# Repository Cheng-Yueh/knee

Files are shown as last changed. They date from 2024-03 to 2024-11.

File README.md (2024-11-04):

# A Multi-Modal, Selectively Lockable, Compact, Affordable Knee Joint Assembly for Bipedal Robots

Welcome to the repository for making your own knee joint concept demonstrator designed specifically for bipedal robots! The files provided here permit reproducing the knee joint as presented in 2024 IEEE-RAS International Conference on Humanoid Robots conference. A video demonstrating the performance of this knee assembly is available at https://youtu.be/-a_vLSxSMBE.

### Key functionalities:
*	Actuated bidirectional joint rotation
*	Disengaged (neutral) or active transmission modes
*	Backdrivable
*	Joint lockable when fully extended, and can remain locked without consuming any energy

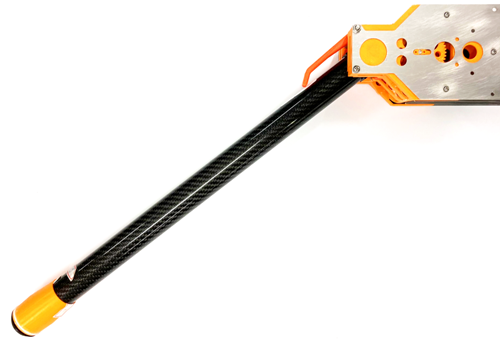
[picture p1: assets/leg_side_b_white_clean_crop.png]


## Mechanical hardware summary
To make things accessible for as many as possible, the design focuses heavily on field deposition modeling (FDM) 3D printable parts using a single extruder. Other items, like specialty parts, are described below. Fasteners are depicted in the CAD model. Mechanical and electronics assembly guidelines are provided separately. Refer [/CAD](CAD/).

### Manufactured parts
These mechanical parts do require workshop fabrication:
| Name (in CAD) | Description | Quantity | Details |
| --- | --- | --- | --- |
| KNEE_BRACE_3 | Chassis plate A | 2 | 1 mm SS304, laser cut |
| KNEE_BRACE_OUTER_V3 | Chassis plate B | 2 | 1 mm SS304, laser cut |
| KNEE_PIN_V3 | Knee lock pin bolt | 1 | SS304, CNC milled |
| KNEE_INNER_2B_V5 | Knee pivot | 1 | AL7050/7075, anodized, CNC milled |

### Bearings and bushings
| Name (in CAD) | Description | Quantity | Details |
| --- | --- | --- | --- |
| SKF - 61803 | Joint ball bearing | 2 | Can use 6803ZZ or alternatives |
| H370FI-0405-06 | Pin bolt sleeve | 1 | IGUS® bushing |
| H370SI-0405-06 | Pin bolt receptacle | 1 | IGUS® bushing installed in knee pivot |

### Actuators
| Name (in CAD) | Description | Quantity | Details |
| --- | --- | --- | --- |
| MOTOR_140 | Type 140 motor | 4 | Mabuchi RE-140RA-12240 or equivalent |
| SOLENOID_SH_K0730 | Latching solenoid | 1 | Shih Shin SH-K0730S-06V |

You will need to source a suitable spring (or two) for the latching solenoid. An example design is provided [here](CAD/SPRING.PDF).

## Electronics summary
Schematics and Gerber files to let you DIY electronics presented in the conference paper are provided in [/electronics](electronics/). The associated Python code (executable on a Raspberry Pi) are available in [/code](code/). Prescribed methods piggyback on 5V I2C communication protocol; remember to include a level shifter if using a Raspberry Pi. Shielded cabling mitigates EMI. However, you can use any method to operate the knee joint. Feel free to adapt and use your own devices if desired.

### Motor and solenoid driver (DRIVER_KNEE_V5)
Select your own feedback current resistor values (R<sub>FB</sub>) corresponding to R_M1 to R_M4 on the schematic. These should be populated – even if you do not intend to measure current. Nominal values provided are for reference only.

### Knee joint angle sensing (ENCODER)
A small radial magnet is necessary to complement this Hall-effect sensor. Adapt the CAD files as necessary for the magnet you acquire.

## Comments or suggestions
[Submit a ticket](https://github.com/Cheng-Yueh/knee/issues)

IMAGE ALT TEXT HERE (https://www.youtube.com/watch?v=-a_vLSxSMBE)

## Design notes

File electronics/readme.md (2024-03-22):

# Electronics
Custom electronics were devised for driving this open source product. Two relevant PCBs are:
*	Joint angle sensor (ENCODER): acquires the absolute angular position of the knee using a Hall-effect IC.
*	Motors and solenoid driver (DRIVER_KNEE_V5): independently maintains constant actuation using built-in PWM functionality. Output current could be estimated on each of the four motor H-bridge channels.

Both devices are managed using I2C (SMBus) protocol. Get your PCB and solder mask made with files in [/GERBER](GERBER/). Reflow soldering is recommended for the surface mount devices. Advise processing bottom layer before top layer. Refer [soldering schematic PDF](Soldering%20Schematics.pdf).

Alternatively, modify and adapt the mechanical CAD model to suit your own electronics as you wish.

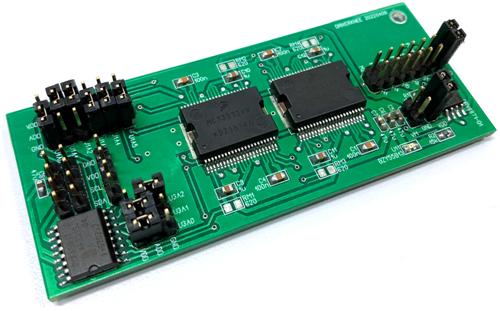
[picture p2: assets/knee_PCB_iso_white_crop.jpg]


## ICs used
The tables exclude passive or connector components.

### DRIVER_KNEE_V5
| IC name  | Description | Footprint | Quantity |
| --- | --- | - | - |
| PCA9685PW  | 16-channel, 12-bit PWM Fm+ I2C-bus LED controller  | TSSOP28 | 1 |
| PCF8591T  | 8-bit A/D and D/A converter  | SO16W | 1 |
| MC33932VW | 5.0 A throttle control H-bridge | HSOP44 | 2 |
| DRV8871-Q1 | 3.6-A Brushed DC Motor Driver With Internal Current Sense (PWM Control) | HSOP8 | 1 |
### ENCODER
| IC name  | Description | Footprint | Quantity |
| --- | --- | - | - |
| AS5048B  | Magnetic Rotary Encoder (14-Bit Angular Position Sensor) | TSSOP14 | 1 |

## DRIVER_KNEE_V5 wiring
Motor [wiring configuration](Wiring%20Configuration.pdf) is separately outlined, which is compatible with the Python code provided. Other connections are tabulated below.

| PCB label | Connect to | Component | Remarks |
| --- | --- | --- | --- |
| M1 to M8 | Motor pins | DC motors | Refer Wiring Configuration.pdf |
| S1 | Red (+) wire | Latching solenoid | Refer manufacturer datasheet |
| S2 | Black (-) wire | Latching solenoid | |
| VM | 12: 24V<br>GND: ground | Power supply | Intended for 12V but 24V compatible |
| VDD | 5: 5V<br>GND: ground | | |
| U1A0 to U1A5 | | Jumpers | Programmable I2C slave address for PCA9685PW |
| U3A0 to U3A3 | | Jumpers | Programmable I2C slave address for PCF8591T  |
| SDA | I2C data line | Computer/ microcontroller | |
| SCL | I2C clock line | Computer/ microcontroller | |
| GND | Ground | | Common I2C and VM ground |

## Caveats
* All electronics could be manually soldered by hand. Any thermal pads underneath ICs must be connected!
* Prepare suitably long cables. Excessive lengths may require I2C capacitance buffers / accelerators. Too short and you will experience poor cable management.
* Plan cable connection points to facilitate modular (dis)assembly.

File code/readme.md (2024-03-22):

# Code overview
The default electronics provided can be operated using a Raspberry Pi using these Python files:
* driver_public.py: drives the actuators (motors and latching solenoid).
* encoder.py: retrieves joint angle readings from AS5048B.
* pcf8591_public.py: retrieves raw ADC values for motor current estimation.

## Usage
Recommended function APIs are documented below; helper functions are not included.

### driver_public.py
#### `initialize(PCA9685_add)`
Initializes the PCA9685PW PWM IC with default settings.

Parameters
*	PCA9685_add(int): I2C address.

Returns None

#### `set_PWM_freq(PCA9685_add, freq)`
Sets the desired PWM frequency of PCA9685PW to drive H-bridges.

Parameters
*	PCA9685_add(int): I2C address.
*	freq(int): PWM frequency in Hz.

Returns None

#### `set_knee(PCA9685_add, func, duty, duty_max = 0.25, duty_lambda = 1, duration = None)`
Actuates the knee motors with specified mode of operation.

Parameters
*	PCA9685_add(int): I2C address.
*	func(int): knee joint operation mode. 0: flexion (bend knee); 1: extension; 2: disengage transmission; 3: engage transmission.
*	duty(float): PWM motor duty (0 to 1).
*	duty_max(float): maximum permissible PWM motor duty (0 to 1) regardless of duty(float).
*	duty_lambda(float): duty prescaler (0 to 1) to impart a net downward compound transmission gear force using differential PWM motor duties.
*	duration(float): operation time in seconds; motors will turn off after duration.

Returns None

#### `set_solenoid(PCA9685_add, mode, duration=0.1, lock_duty = 1.0, unlock_duty = 0.5)`
Actuates the latching solenoid knee lock.

Parameters
*	PCA9685_add(int): I2C address.
*	mode(int): 0: lock; 1: unlock.
*	duration(float): operation time in seconds; solenoid will turn off after duration.
*	lock_duty(float): lock mode PWM duty (0 to 1).
*	unlock_duty(float): unlock mode PWM duty (0 to 1).

Returns None

### encoder.py
#### `read_angle(output = 'bit', offset = 0, remap = True, enc_add = ENC_ADD)`
Returns the absolute knee joint angle.

Parameters
*	output(str): 'bit': returns angle in raw bit value; ‘deg’: returns angle in degrees; ‘rad’: returns angle in radians.
*	offset(float): returns the angle relative to a prescribed offset value.
*	remap(bool): True: remaps angle equivalent to -180° < value ≤ 180°.
*	enc_add(int): I2C address.

Returns int if output == ‘bit’, else float

### pcf8591_public.py
#### `set_mode(auto_inc = None, channel = None, PCF8591_add = PCF8591_ADD)`
Initializes the ADC scanning mode, and returns the associated configuration mode value.

Parameters
*	auto_inc(bool): True: sets ADC to automatically increment return values over each channel as defined in IC datasheet; False or None: disables ADC auto increment.
*	channel(int): sets a single ADC channel (0 to 3) for returning values. Refer to IC datasheet.
*	PCF8591_add(int): I2C address.

Returns int

#### `get_adc_values(mode = MODE, n = 1, PCF8591_add = PCF8591_ADD)`
Reads and returns ADC values.

Parameters
*	mode(int): ADC scanning mode configuration value.
*	n(int): number of times to read the ADC with defined mode.
*	PCF8591_add(int): I2C address.

Returns list

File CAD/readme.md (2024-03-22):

# Mechanical assembly
The prescribed assembly is available as Parasolid format (LEG_ASSY_2_PUBLIC.x_t). Construction order should be quite self-explanatory; there is no single best method, which lends to modular flexibility. In general:
*	Prepare ALL electronics and wiring in advance.
*	Build the knee joint from inside core to the outside.
*	Use various strength threadlocker (or none at all) in lieu of nyloc nuts.
*	Cable conduits and holes throughout the CAD model facilitate different wiring combinations depending on application. Use them wisely.

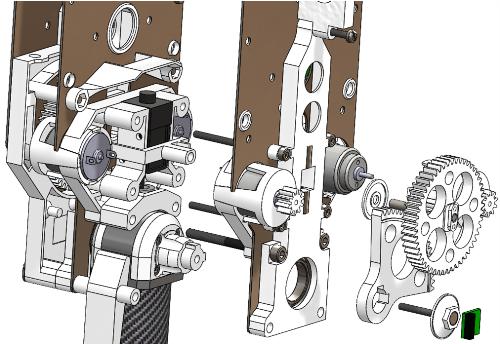
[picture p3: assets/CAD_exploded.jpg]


## FDM suggestions
Field deposition modeling (FDM) for 3D printing plastic parts presented in this product is preferred. Ultraviolet stereolithography (SLA) methods are not advised due to poor structural strength. 30% infill using polylactic acid (PLA) should be more than adequate for most parts. Consider up to 60% infill for knee pivot components experiencing concentrated stresses.

## Lubrication
All transmission components should be lubricated with elastomer-polytetrafluoroethylene gelling agent and parafiinic mineral base oils. These grease compounds do not react with FDM plastics such as PLA, facilitating stable and low maintenance operation.

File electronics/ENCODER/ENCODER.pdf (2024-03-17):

VDD5V

1
2

1

### 2 U2 HEADER2

C1 47u

## Cheng-Yueh Liu ENCODER rev: 15 March 2024

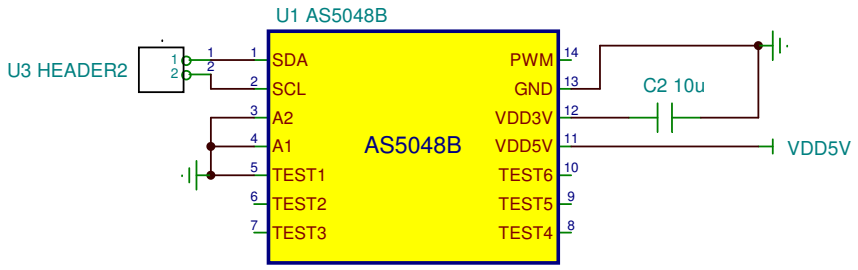
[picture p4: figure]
VDD5V; U3 HEADER2; PWM; GND; VDD3V; TEST6; TEST5; TEST4; SDA; SCL; TEST1; TEST2; TEST3

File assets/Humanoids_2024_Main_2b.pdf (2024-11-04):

On the Development of a Multi-Modal, Selectively Lockable, Compact,

## Affordable Knee Joint Assembly for Bipedal Robots

Cheng-Yueh Liu¹

, Jaspreet S. Dhupia¹

, Minas Liarokapis¹

, and Pei-Chun Lin²

Abstract— Contemporary advances in humanoid bipeds include complicated mechanisms supporting fully actuated robotics. While these solutions offer unprecedented versatility that relies on sophisticated locomotion systems, the efficient traversing capabilities of natural, passive-inspired gait may be overlooked. In this paper, we focus on the development of a disengage-able, selectively lockable, affordable knee joint assembly suitable for either active or underactuated biped operation. The multi-modal nature of the design facilitates actuated bidirectional rotation as well as disengaged operation, while the knee lock ensures legs remain rigid during stance phase. Experimental validation of the performance of the knee assembly demonstrated both controllable knee joint actuation and fully passive rotation, various modes of operation, and torque evaluations. Further investigations include validation testing of operational and locking performance on a physical bipedal robot. System parameter optimizations can reduce energy consumption. The design proved feasible and is opensourced to facilitate replication and co-development with others.

I. INTRODUCTION

Bipedal robots are characterized by an unparalleled versatility, leveraging their advanced human-like locomotion capabilities that allow them to traverse dynamic and unstructured human-oriented environments. These systems must include a mechanism that reduces effective hip-foot length. A knee joint mechanism provides such capability in humanoids, which is essential to prevent foot scuffing during leg swing phase. The rear leg can rotate forward without the feet hitting the ground. However, many implementations try to achieve the most overpowered solution for utmost capability, which obfuscates elegance and basic requirements in simple bipedal gait. Through appreciating fundamental paradigms, the proposed knee supports first principles evaluation and potential transfer of natural human gait for efficient robot walking. A simple and low cost design promotes mass replication and widespread adoption within the robotics community.
A basic kneed walker could be modelled as a planar biped depicted in Figure 3. An upper body linkage manipulates robot center of mass (CoM) in the sagittal plane to initiate gait. Such configuration biomimics human physiology and can be considered as a template in biped robotics development. Although different postures during walking are possible, the most fundamental gait in Figure 2 provides a basis for which variations could be built upon. Under these

1Cheng-Yueh Liu, Jaspreet S. Dhupia, and Minas Liarokapis are with the Department of Mechanical and Mechatronics Engineering, The University of Auckland. Emails: cliu695@aucklanduni.ac.nz, j.dhupia@auckland.ac.nz, minas.liarokapis@auckland.ac.nz
2Pei-Chun Lin is with the Department of Mechanical Engineering, National Taiwan University, Taiwan, ROC. Email: peichunlin@ntu.edu.tw

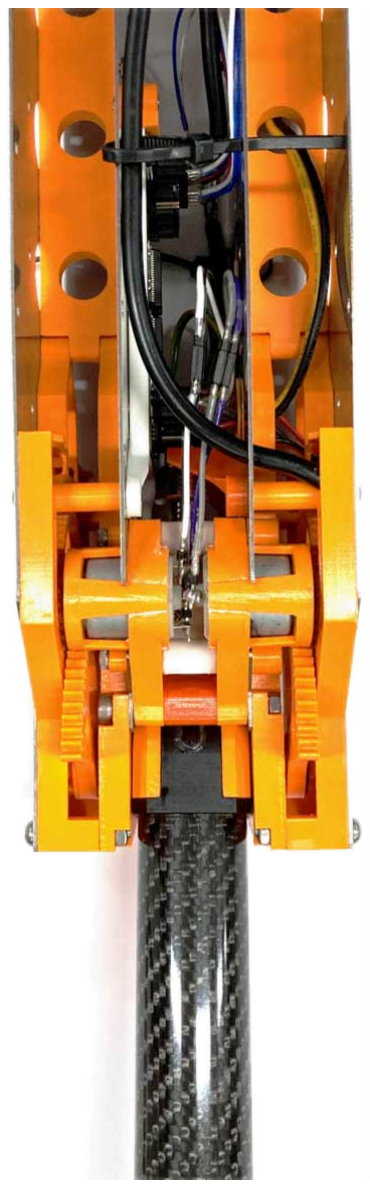
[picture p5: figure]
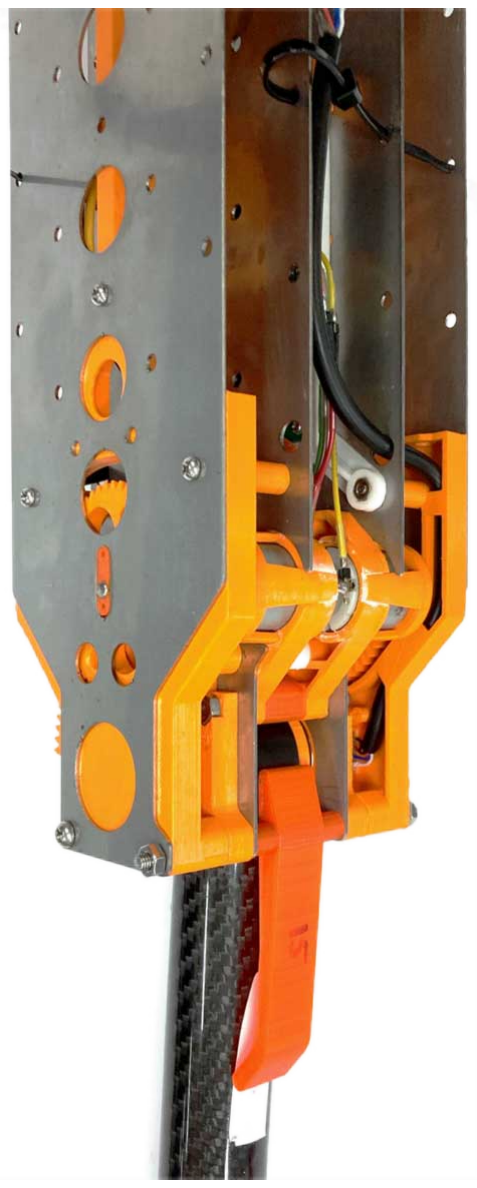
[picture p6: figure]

Fig. 1. The proposed knee joint assembly. Subfigure a) presents the rear view and subfigure d) presents the isometric view. All associated mechanisms, actuators, and electronics presented throughout the paper are integrated within the depicted assembly. The near symmetrical layout across both sagittal and coronal planes, facilitates an even distribution of inertia and mass.

circumstances, the knee of stance (dotted) leg remains locked and rigid.
Therefore, the sole purpose for knee bends of the rear swing leg is preventing foot scuffing. Such gaits do not require knees to exert much torque (if any) requiring little actuation. This effect is further accentuated should lower limb extremities, consisting of shank and foot, possess minimal mass and rotational inertia about the knee.
The Lagrange dynamic model describing biped motion of the configuration in Figure 3 is found to be
D(θ)θ¨ + h(θ, θ˙) + G(θ) = τ | (1)

where
θ | = [θ1, θ2, ..., θ5]

T
,
τ | = [τθ1, τθ2, ..., τθ5] | T ,

h(θ, θ˙) = col[
P
| 5
| j=1(j̸=i)

(hijj (

| | ˙θj )
| | 2
],
G(θ) | = col[Gi(θ)],
D(θ) | = [Dij (θ)], | i, j = 1, 2, ..., 5.

(2)

Here D(θ) is the 5 × 5 symmetric, positive definite

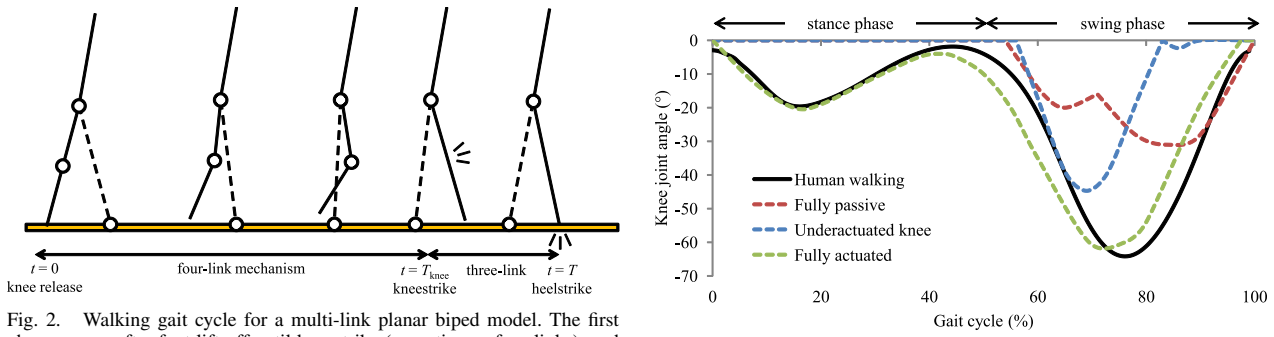
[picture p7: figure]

Fig. 2. Walking gait cycle for a multi-link planar biped model. The first phase occurs after foot lift-off until kneestrike (operating as four links), and the second phase continues until heelstrike as a two-link mechanism.

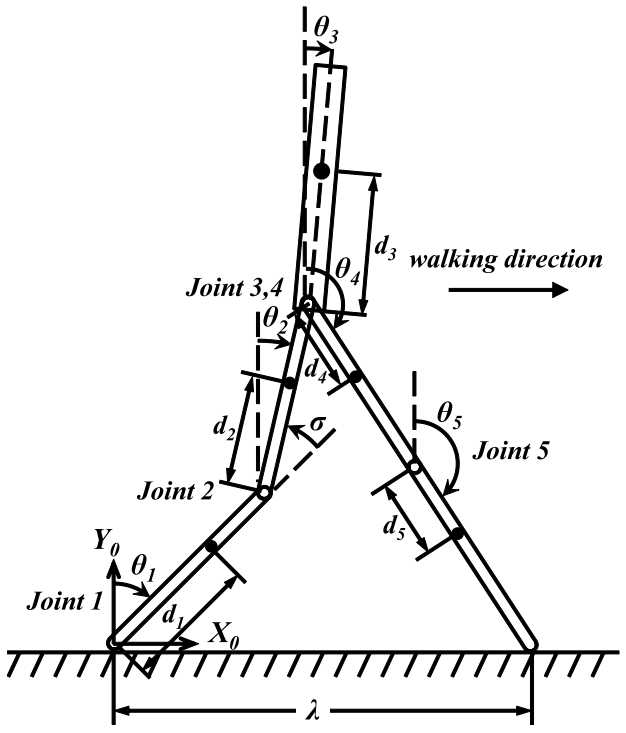
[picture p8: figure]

Fig. 3. Nomenclature of a 5-link planar biped robot suitable for the proposed knee joint. By manipulating upper body angle θ3, the robot can commence walking when center of mass is ahead of stance (front) foot.

inertia matrix, h(θ, θ˙) is the 5 × 1 vector of centripetal and Coriolis forces, G(θ) is the 5 × 1 vector representing gravitational forces, and τ is the 5 × 1 generalized torque vector corresponding to θi
. A full derivation [1] and equations during heel and knee strike switching events [2] are well documented.
Figure 4 portrays generalised knee angles, which never exceed -70°, during comfortable human walking and compares that with various biped setups. Physiologically, the human knee does undergo slight flexion during stance. Passive dynamic walkers can be classed as legged machines for which dynamic walking occurs naturally. By offering a clutch for transmission engagement and disengagement, natural bipedal dynamics can be combined easily with active energy input so as to produce efficient and versatile walking over

Fig. 4. Representative knee angles of human vs select biped robot topologies during walking. Flexion angles are negative. Comfortable human walking speed = 1.24 m/s, stride length (2λ) = 1.32 m. Graph constructed as a composition from existing graphs in [3]–[5]; human knee flexion angles collated using averages of comfortable gait data in [6].

a broad range of unstructured terrains [7]. Another category of simple walking machines, underactuated bipeds, can take advantage of upper-body control, resulting in efficient limitcycle gaits by avoiding generation of negative input power [8]. Moreover, robots that harness passive dynamics use less control and energy than other powered robots, yet walk more naturally [9]. Through actively controlling the hip, knee joints can be underactuated during the locomotive gait. Previous underactuated or passive dynamic walkers lock their knees straight throughout stance phase. Table I provides an overview of knee functionalities in fully passive, underactuated and fully actuated biped setups. In [10] Etoundi, et al. reviewed various biomimicking knee joints and identified general trends. For example, a bio-inspired knee joint incorporated planetary gearing with pneumatic artificial muscles actuating a compound sun gear pulley [11]. Another design consists of a crossed four-bar linkage with variable transmission and a joint stop proposed in [12]. The remainder of this paper is organized as follows: Section II divulges on the inspiration behind the mechanical design, Section III discusses in detail how the proposed transmission mechanism works and custom electronics, Section IV presents the experimental validation of the efficiency of the proposed knee assembly, while Section V concludes the paper and discusses future directions.

II. DESIGN INTENT

A disengageable transmission facilitates controlled passive walking. For the most elementary geared knee clutch, the decoupling of joints to any actuation transmission enables underactuation and exhibit passive dynamics [19]. Such natural movements form an ideal scenario whereby a robot could harness the ultimate manifestation of energy efficiency, coupled with a fully actuated or backdrivable joint when necessary.
Hip joint actuation is by far the main power contributor for sustaining forward gait locomotion [8], [9]. In this context, it is feasible to derate (or underpower) the knee joint as much as possible. The knee need not contribute torque for forward motion and can be locked during stance. Positioning the knee

TABLE I

VARIOUS KNEE ACTUATION TOPOLOGIES FOR A HUMAN-INSPIRED WALKER.

Type | Fully passive | Underactuated knee | Fully actuated

Example image

Description | Passive dynamic walkers walks down slope without any actuation. Powered by gravity. | Robot with passive-inspired elements and actuated hip. Walks on flat sur-face. | All relevant degrees of freedom are actively controlled with actuators, in-cluding knees and hip joints.
Select examples | Dexter, robots by Garcia/McGeer, Ru-ina/Collins [3], [7], [9] | Dribbel, Denise [13], [14] | ASIMO, Atlas, NAO, Veronica, RoK-4 etc. [15]–[17]
Knee design | No active actuation. Knee flex-ion/extension occurs naturally during gait. | Active knee locking mechanism. Knee rotation not actuated. | Knee joint directly actuated via per-manent transmission. May use adapt-able or compliant joints. [18]
Angle range | 0° to -35° typ | 0° to -50° typ | 0° to -65° typ
Knee torque performance | 0 Nm | 0 Nm | Varies greatly depending on robot.
Knee lock | May incorporate passive knee locking mechanism for stance phase. | Electromagnetic, voice-coil, motor or solenoid driven etc. | Under-actuated examples plus clutch variations coupled to active transmis-sion.
Passive mode | Yes | Yes | No
Controllable flexion | No | No | Yes

TABLE II

KNEE DESIGN SUMMARY AND PHYSICAL PARAMETERS OF TEST SHANK.

| Variable | Value
Angle range | -σ | 0° to -70°
Knee lock | | Latching solenoid
Mechanism mass | | 470 g
Passive mode | | Yes
Controllable flexion | | Yes
Shank length | d1 + d5 | 0.45 m
Shank mass | (Link 1) | 0.09 kg
Foot mass | Joint 1 | 0.04 kg
Moment of inertia about knee | | 0.0142 kg m²
Shank CoM | d1 | 0.1558 m

actuators nearer the hip with mechanisms, such as linkages or cables, for transmission [20] add complexity and mass. A lightweight knee joint reduces overall leg mass and inertia, which facilitates smaller hip joint torque requirements. During the stance phase, each knee must able to support its corresponding thigh, hip, and swing leg without bending. Such substantial loading would require knee exertion of significant torques during what should be a passive gait phase.

One straightforward actuation methodology is to mount a geared, inline motor directly at the knee joint with supporting elastic and damping elements [21]. However, with no locking mechanisms, energy is consumed to oppose bending torques using the employed actuator. Instead of relying on actuators, a separate knee locking mechanism, which does not consume energy to maintain state, is desirable. Plooij, et al. [18] identified properties an ideal robot joint locking device shall possess: i) adjustable locking directions, ii) ability to unlock while under load, iii) low energy consumption, iv) ability to lock in any position, v) short switching time, vi) high locking force and vii) be compact, lightweight, and inexpensive. Locks could be categorized by active or passive modes of operation, which include electromagnetic [22], permanent magnet [23] or the use of suction cups for lock activation. Reynolds [24] developed a differential-brake style clutch. However, passive knee locking mechanisms could lose synchronization with the gait cycle that can affect overall reliability.

III. MECHANISM DESIGN

A large speed reduction ratio is necessary to provide sufficient torque for actuating robot shanks [25]. The solution presented here uses a multistage gear reduction system incorporating a compound gear for an overall 40:1 gear reduction. The hardware is composed of subsystems incorporating a gearbox, lock, associated electronic drivers, and a rotary encoder (see Figure 5). The knee joint is actuated using

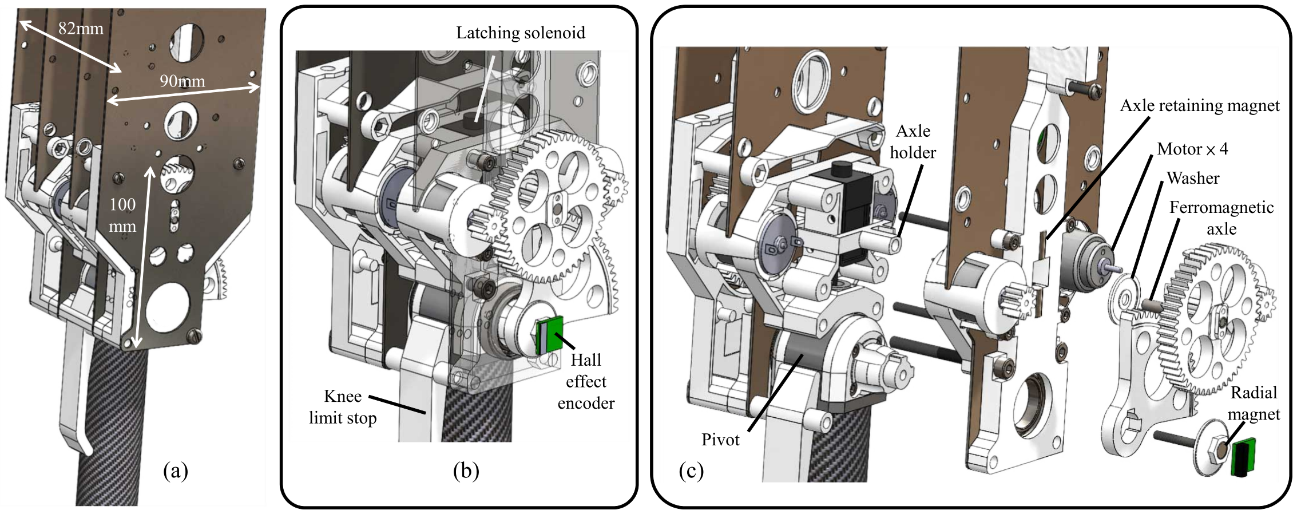
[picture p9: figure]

Fig. 5. Knee joint mechanism. Mass is 470g excluding chassis components. a) Overview. b) Cutaway view without side sheetmetal. c) Exploded view of left half, revealing axle holder, which can translate vertically about the latching solenoid in the inner core. Mechanism is symmetrical about sagittal plane.

a modified planetary gearbox transmission system that can
be disengaged for passive dynamics. An embedded bolt,
powered by a bistable or latching solenoid, keeps the shank either locked at a fixed angle (during stance phase) or unlocked without consuming any energy to maintain state (see Figure 6).
Serial elastic actuation elements were considered but omitted. Low transmission torque outputs mean elastic components must be soft, implying minuscule energy storage is obtainable. However, damping elements could be retrofitted to smooth stroke transitions at end limits.
A. Gearbox
In the proposed design, Type 140 brushed direct current (DC) motors, rated at 6V (Mabuchi RE140RA-12240 or equivalents), provide knee joint power at 80 g each. Four motors are arranged in a planetary fashion as depicted in Figure 6, without ring gear. Coupled to a compound sun gear, the two-stage transmission imparts a gear reduction of 50:10 and 80:10 respectively. Furthermore, each pair of motors is symmetrically positioned in both the sagittal and transverse planes. This deliberate organization ensures the mechanism imparts identical inertial distribution across both planes while promoting equal torque contribution from each motor.
B. Gearbox Doubles as Clutch
Each compound (sun) gear revolves between two, significantly smaller, planet gears placed diametrically opposite and horizontally 180° apart. Rotating the compound gear about a fixed axle transmits torque to bend the knee in either direction, which is achieved by synchronous operation of all four DC motors in tandem and rotating the joint. However, the transmission is deliberately designed so other modes of operation are possible if minor constraints are removed. When the sun gear axle is permitted to translate vertically upwards, by a lateral displacement marginally greater than the gear tooth depth, the compound gear is decoupled from the output (second gear set). This additional degree of freedom can be employed by contra-rotating the two planets in opposite directions. It is important to ensure the sun gear movement is restrained such that the teeth always mesh with planet gears. Therefore, four modes of operation become possible: i) transmission disengagement, ii) transmission engagement, iii) clockwise join actuation, and iv) counterclockwise joint actuation. Retaining the sun gear axle in the up or down position, for transmission disengagement or engagement respectively, can be achieved by any methodology deemed suitable in the actual application. For the purposes of this paper, permanent magnets are used in conjunction with a ferromagnetic axle. The two motors could also impart net up or down translational forces so as to assist in retaining the sun gear position. For example, when the axle is in down (engaged) position for knee rotation, both planet gears (and motors) are actuating in the same direction. Due to being positioned opposite each other, one of the planets will be invoking an upwards force when driving the sun gear teeth, but neutralized by the other planet exerting force downwards. By applying not only various voltages or duties, but also a differential, to the two motors while actuating the joint, both the net output torque and sun gear retaining force can be adjusted. By repurposing the very motors and gears used for joint actuation, the gearbox effectively doubles as a clutch. Simple yet innovative supplementary mechanics are important when pursuing elegant outcomes.
C. Joint Lock
Electromagnets or voice-coil actuated locks [13] consume substantial current (up to a few amperes) just to maintain state. A miniature latching solenoid (Shih Shin SH-K0730S-06V) [26] was identified so as to implement a linear boltlock configuration. These devices passively maintain a set position without constant application of electrical current. The latching solenoid linearly actuates a 6.3 mm bolt into the joint pivot, with 9 mm stroke for locking (Figure 6c).

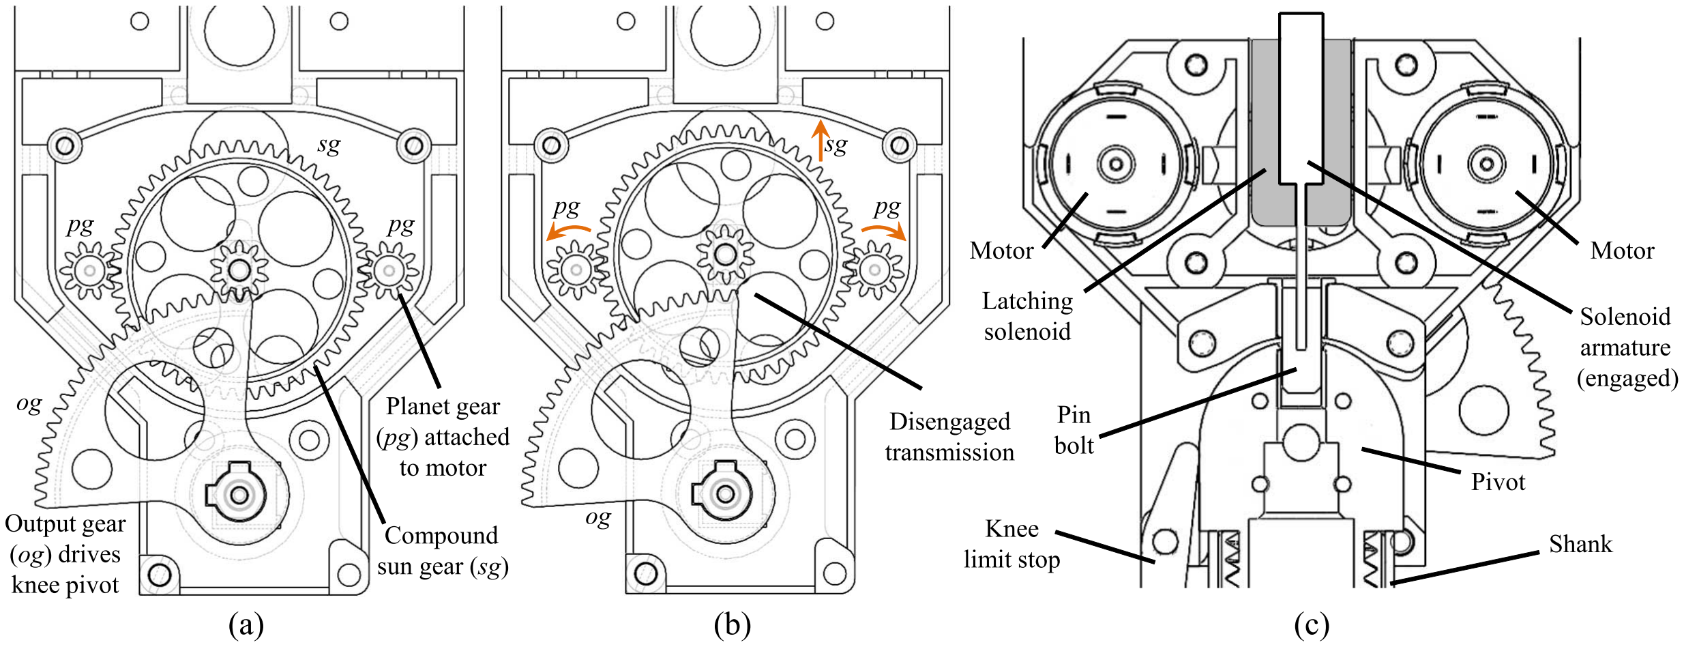
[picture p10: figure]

Fig. 6. Gearbox and knee lock. a) Engaged transmission; compound sun gear (sg) is down and mating with output gear (og) of knee pivot. b) Disengaged transmission; sg is up and floats above og. c) Knee lock mechanism with pin bolt engaged, preventing the pivot from rotating. The cross section is across lower limb sagittal plane.

TABLE III

KNEE DRIVER LOAD CURRENT ESTIMATION FOR SELECTED RF B .

RF B

aADC
(10⁻³)

bPWM

cconst
(10⁻³)

R

| | | | 2 | RMSE (10⁻³) | RSE (10⁻³)
4k7 | 1.09244 | 0.23724 | -10.9677 | 0.9972 | 4.6597 | 4.8732
10k | 0.52400 | 0.17088 | -7.80886 | 0.9997 | 0.9922 | 1.0501
22k | 0.24959 | 0.24924 | 2.80037 | 0.9997 | 1.1807 | 1.2623

To minimize friction and assist engagement, the pivot is press-fitted with an IGUS® H370SI-0405-06 self lubricated bushing which acts as the receptacle. A secondary IGUS® H370FI-0405-06 bushing supports the bolt on the fixed side. In practice, the fully assembled joint exhibits a maximum backlash of approximately 5° when locked. Liu, et al. [27] devised a tapered pin lock configuration, the shape of which removes fit clearance to prevent knee bending when engaged. Such provision for compliance is a reference for further mechanical refinements.

In order to actuate the aforementioned electromechanical DC motors and solenoids, custom made knee driver electronics have been developed. Programmable resistor/capacitor combinations, as described in the evaluation section below, generate voltages that estimate feedback current sensing characteristics of the four DC motors. An 8-bit analogue to digital converter (ADC) reads the associated voltage. Both the PWM generator IC and ADC employ I2C for data communications with the microcontroller unit. Finally, a 14 bit Hall-effect rotary encoder (AS5048) about the knee joint axis of rotation measures knee stance angle. A radial magnet is placed on one end a rotating axle (hidden), adjacent to the encoder. I2C interface is used throughout for bus commonality.

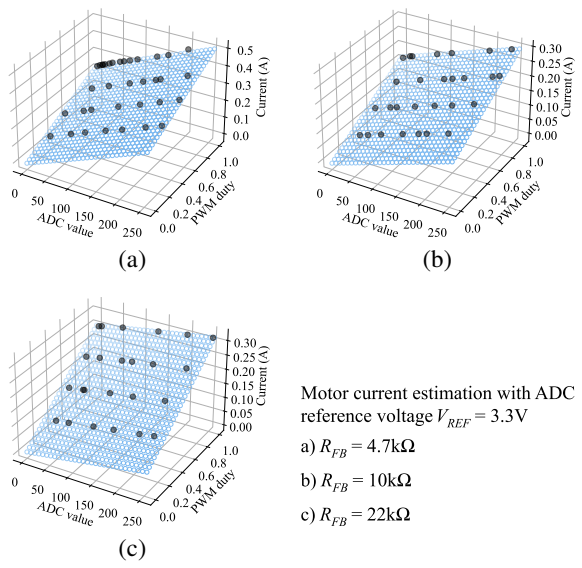
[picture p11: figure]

Fig. 7. Knee driver current sensing calibration with various feedback resistors (RF B). By choosing an appropriate value, full scale detection of motor current can be realized.

IV. EVALUATION

The proposed knee joint assembly is depicted in Figure 1. The shank (attached to the joint) is a carbon-fiber tube with a plastic “shoe” (see Figure 10). Apart from electromechanical actuators, knee pivot and bolt lock, all other mechanical parts are printed with fused deposition modeling using polylactic acid (PLA). Shank parameters and knee joint costings are listed in Tables II and IV respectively.

A. Motor Driver and Current Sensing

The knee motor driver PCB incorporates 8-bit current sensing capabilities. Current sensing calibration is required

TABLE IV

LISTED COST BREAKDOWN FOR ONE KNEE MECHANISM.

Item | USD
PLA material | 2
DC motors (four) | 8
Latching solenoid | 12
SS304 lock pin bolt (CNC) | 30
AL7075 knee pivot (CNC) | 180
Bearings | 15
Electronics | 60
Miscellaneous | 5
Total | 312

to understand the relationship between ADC readings, H-bridge PWM duty cycles, and actual (motor) load current for programmable current sensing resistor values (RF B). In this paper, tests were conducted with 1526Hz PWM frequency and slow decay (low side active freewheeling). Variable loads are connected directly to one knee driver H-bridge output with a multimeter in series. Results for RF B = 4.7k, 10k and 22k Ω are depicted in Figure 7.
Optimal RF B selection should produce full-scale ADC readings (0 to 255) across a range of expected load currents. For each scenario, a multiple linear regression is conducted by treating ADC value, PWM duty and load current as independent variables. Table III lists the multiple linear regression results including correlation coefficients:

Iload = aADC ADC + bPWMPWM + cconst (3)

where Iload, ADC and PWM are the measured load current, raw ADC values and PWM duty cycle respectively. Selecting a sensible RF B value necessitates coordination with experimental gait requirements to be conducted in the future.

B. Joint Lock

The latching solenoid disengagement is provided by compression springs. When compressed, these must exert less force than the solenoid’s 8 N permanent magnet latching force. Liberal lubrication is applied to lock contact surfaces, which is necessary for successful operations. Unimpeded lock transition takes roughly 0.2 s.
1) Unlocking: During disengagement, maximum spring (ejection) force occurs when there is net zero magnetic flux in the solenoid armature, which is afforded by a reverse current of 1 A at 8 V. Please note that there is some backlash between the bolt and the receptacle. During level walking, knee unlocking and bending only occurs during swing phase and the motors never need to overcome torque, induced by weight above the joint, in the locked stance phase.
2) Locking: On the contrary, a larger forward current results in greater interim latching force for compressing the

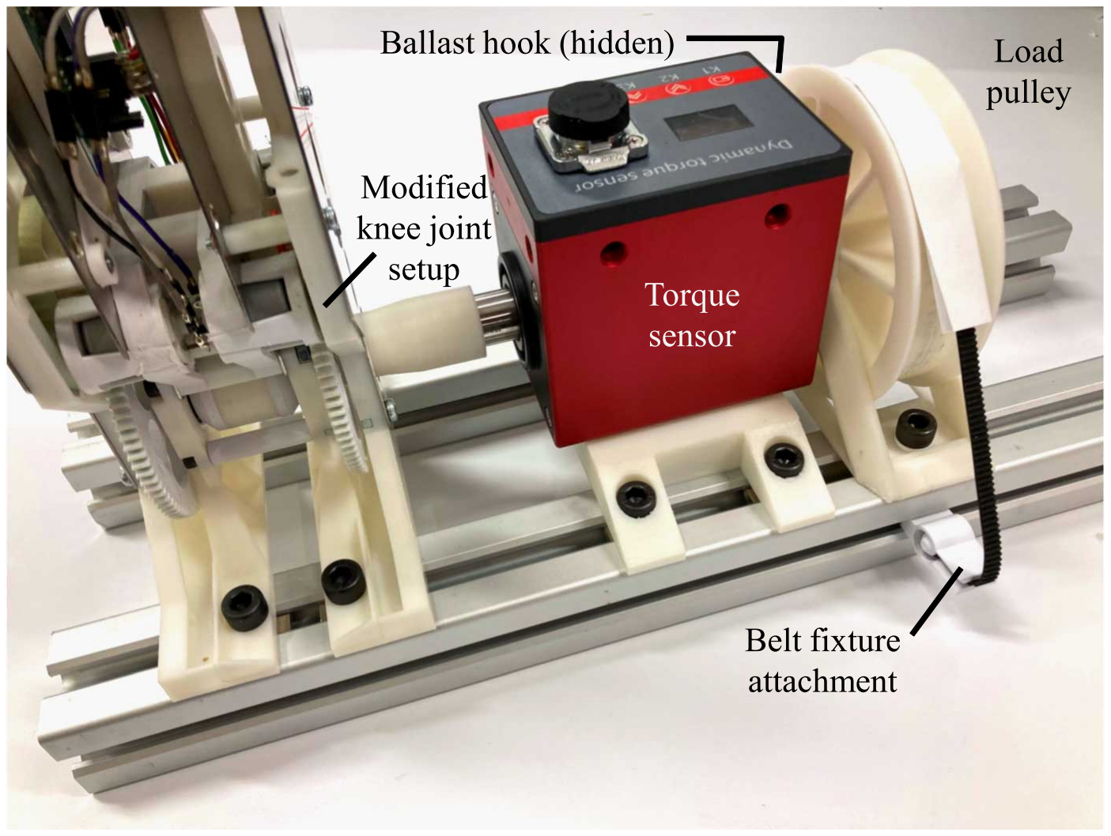
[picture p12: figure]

Fig. 8. Knee joint torque evaluation setup. A CALT DYN-200 sensor is serially attached to the output of a modified joint setup. Load pulley and ballast weight acts as friction device for generating resistive torque.

spring. Therefore, maximum current can be applied for the shortest duration possible. In practice, lock activation during joint rotation means that the bolt rubs against the pivot until it engages the receptacle upon alignment. Heat dissipation should be alleviated. In order to maximize their active duty, solenoids should be mounted to the chassis via a thermally conductive bracket.

C. Gearbox Clutch Mode
Given appropriate motor driver commands, various function modes can be triggered as intended. An important observation is that sun gear dislodgement can occur if there is sufficient obstruction that impedes free rotation of the joint output. This means that transmission could be automatically disengaged if knee joint fails to turn during gear rotation, which is an unintentional consequence of the selected design. Thus, the sun gear must be adequately retained with sufficient locking force to prevent unintended decoupling during operation. Methods that could be employed include selecting suitable spring clips and permanent magnets.
D. Torque Performance
Certain modifications are conducted for mounting a duplicate device onto a torque test rig (see Figure 8). Instead of rotating a shank, one end of a CALT DYN-200 torque sensor is directly coupled to the output of the knee joint. The other end is connected to a torque load generator. A 110 mm pulley, supporting ballast off a belt, is attached as the load. One end of the belt wraps around the pulley and is fixed to the setup frame. A piece of 80 gsm photocopy paper envelops the belt at the pulley contact area. By changing ballast mass hanging off the belt, the radial and friction force and hence resistive torque from the paper-pulley interface is varied. In order to maintain consistent load torques, the pulley is rotated in the direction that prevents upward force being exerted on the ballast.
Reasonable PWM duties at 24 V were applied to the motor driver board. Various speed-torque performances are depicted

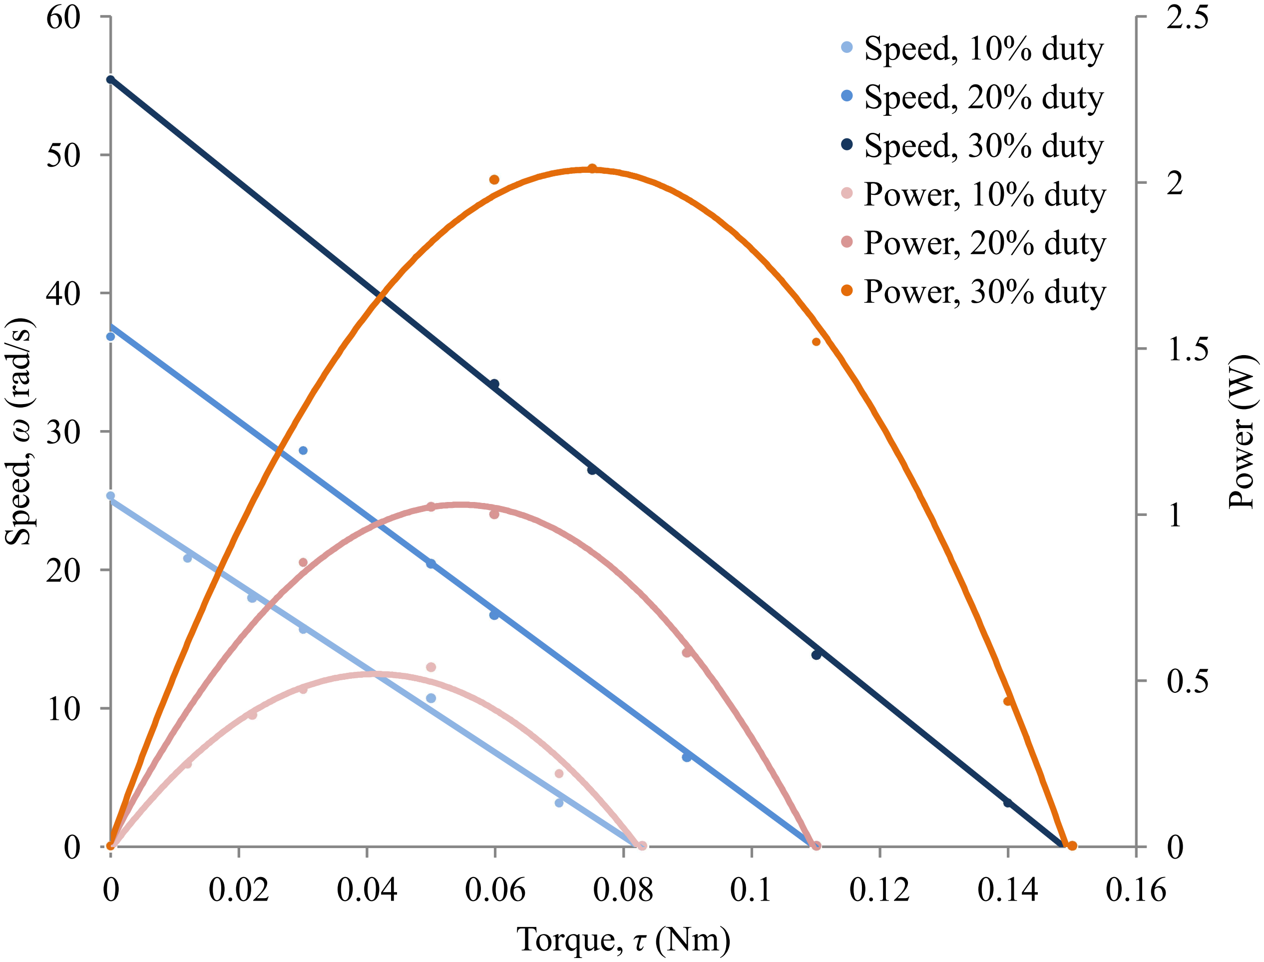
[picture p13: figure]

Fig. 9. Knee joint performance under various loads. Duty cycles up to 30% were evaluated, which gives an acceptable range of speed-torque characteristics.

TABLE V

JOINT PERFORMANCE LINEAR REGRESSION ESTIMATION.

Duty
(%)

∆ω
∆τ

(

rad
Nms )

ωτ = 0
(rad/s) | R
2 | RMSE | RSE
10 | -303.37124 | 25.00549 | 0.9965 | 0.5125 | 0.6064
20 | -342.23120 | 37.57943 | 0.9975 | 0.6214 | 0.7610
30 | -373.02770 | 55.46222 | 0.9996 | 0.3811 | 0.4668

and listed in Figure 9 and Table V respectively. Steady state readings between trials are logged. The setup was left to cool down at room temperature for a minute after each trial. Furthermore, the ballast load is removed and reset between trials to mitigate steady state error.
The system essentially consumes a constant current (at 24
V) regardless of speed/torque for each duty (10%, 0.85 A; 20%, 1.68 A; 30%, 2.6 A). Substantial energy overheads may be present as a constant cost of actuation in the transmission setup, suggesting limited system efficiency.
E. Knee Rotation

The knee, installed into a robotic lower limb assembly, is verified with a proportional-integral-derivative (PID) controller running at 20 Hz. The leg thigh is fixed horizontally for reference and all knee joint angles are measured in degrees and clockwise relative to fully extended shank position (see Figure 10). Sample test scenarios are depicted in Figure
11. Given prescribed gains, the setup is capable of attaining 0.6 s settling time between -67° and -27° with 2° steady state error. This corresponds to 40° flexion from a combined swing and stance angle of 23° in gait without considering thigh dynamics during walking. In bipeds, hip actuation during leg swings passively contributes to shank dynamics in an underactuated manner. Test results demonstrate the feasibility of employing the knee joint design in a biped and warrants further development. Results suggest the following:
- Based on knee angle during the proposed gait cycle (Figure 4), the flexion range of proposed knee mechanism meets or exceeds performance of comparable passive or underactuated walkers. However, in practice, any flexion angle is permissible as long as foot scuffing is avoided.
- Torque requirements are sufficiently small to swing the lightweight shank, which limits the loading imparted on knee actuation and supports rapid flexion or extension.
F. Open-Source Dissemination
All the files that allow replication of the multi-modal, selectively lockable, compact, affordable knee joint assembly are publicly available at the following URL:

https://github.com/Cheng-Yueh/knee

A video demonstration of the performance of the proposed knee assembly can be found at the following URL:

https://youtu.be/-a_vLSxSMBE

V. CONCLUSION AND FUTURE WORK
In this paper, various typologies of active knee joints developed for biped robots were reviewed. Desirable characteristics include options for both active and passive modes of joint operation, lightweight mechanisms, and a disciplined strategy to lock and unlock the knee during swing phase. Ideally, the latter offers active toggling but maintains state without energy consumption. The capability of arbitrarily (dis)engaging transmission can be used to fulfil passive dynamic inspired humanoid gait where possible, while permitting controlled knee actuation when necessary. This unique capability can promote natural gait development for research in efficient biped robots.
These traits form a minimalistic and novel solution for enabling passive, underactuated and driven capabilities that remains locked during stance phase. A multistage arrangement with planet gears provides not only joint rotation, but also acts as a clutch that can actively engage or disengage transmission. In lieu of electromagnets or passive suction cups, latching solenoids offer a knee lock solution that can be actively toggled without consuming current to maintain state. Together, these modular integrations manifests many ideal attributes a biped robot knee joint should possess. Knee joint validation on a walking bipedal robot will be necessary. Locking performance, like anti-moment torque capability, energy consumption details, and options to lock at arbitrary angles demands evaluation. Fine tuning mechanical elements, incorporating dampers, and motor driver parameters is essential for improving energy efficiency. Opportunities remain in refining closed-loop methodologies beyond the rudimentary PID controller presented. The design deliberately facilitates underactuation for controlled yet efficient biped walking in future development.

ACKNOWLEDGMENT
This work is partially supported by the National Science and Technology Council, Taiwan, under contract: MOST 110-2221-E-002-111-MY3.

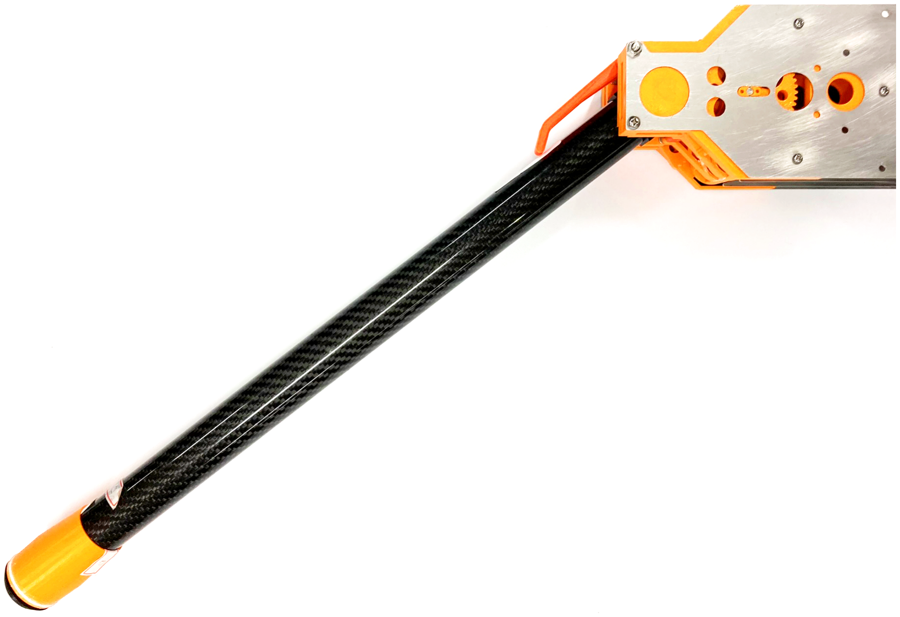
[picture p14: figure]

Fig. 10. Side view of a complete assembled robot leg that incorporates the proposed knee assembly. The thigh is fixed horizontally such that the shank is free to swing. A carbon fiber tube is used for the leg development while the knee assembly uses a combination of metal and 3D printed parts.

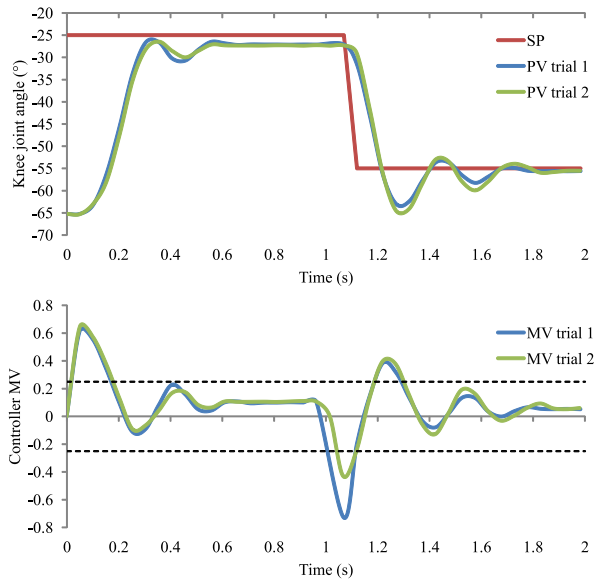
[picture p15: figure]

Fig. 11. Knee-shank actuation with PID (kp, ki, kd = 0.015, 0.008, 0.00125). Set point (SP), present value (PV) knee joint angles and controller outputs (MV) are plotted. MV clipped to ±0.25 for PWM duty.

REFERENCES

[1] S. Tzafestas, M. Raibert, and C. Tzafestas, “Robust sliding-mode control applied to a 5-link biped robot,” Journal of intelligent & robotic systems, vol. 15, no. 1, pp. 67–133, 1996.
[2] E. Borzova and Y. Hurmuzlu, “Passively walking five-link robot,” Automatica (Oxford), vol. 40, no. 4, pp. 621–629, 2004.
[3] K. Rushdi, D. Koop, and C. Q. Wu, “Experimental studies on passive dynamic bipedal walking,” Robotics and Autonomous Systems, vol. 62, no. 4, pp. 446–455, 2014.
[4] V. Duindam and S. Stramigioli, “Modeling and control for efficient bipedal walking robots - a port-based approach,” Springer Tracts in Advanced Robotics, vol. 53, p. 156, January 2009.
[5] A. Maiorino and G. G. Muscolo, “Biped robots with compliant joints for walking and running performance growing,” Frontiers in Mechanical Engineering, vol. 6, 2020.
[6] R. Senden, R. Marcellis, P. Willems, M. Witlox, and K. Meijer, “Normative 3d gait data of healthy adults walking at three different speeds on an instrumented treadmill in virtual reality,” Data in Brief, vol. 53, p. 110230, 2024.
[7] T. McGeer, “Passive dynamic walking,” The International Journal of Robotics Research, vol. 9, no. 2, pp. 62–82, 1990.
[8] F. Asano, “High-speed stealth walking of underactuated biped utilizing effects of upper-body control and semicircular feet,” in 2018 IEEE/RSJ International Conference on Intelligent Robots and Systems (IROS). IEEE Press, 2018, p. 4375–4380.
[9] S. Collins, A. Ruina, R. Tedrake, and M. Wisse, “Efficient bipedal robots based on passive-dynamic walkers,” Science, vol. 307, no. 5712, pp. 1082–1085, 2005.
[10] A. C. Etoundi, C. L. Semasinghe, S. Agrawal, A. Dobner, and
A. Jafari, “Bio-inspired knee joint: Trends in the hardware systems development,” Frontiers in Robotics and AI, vol. 8, 2021.
[11] Y. Liu, X. Zang, Z. Lin, X. Liu, and J. Zhao, “A bio-inspired knee joint for biped robots,” in 2016 IEEE International Conference on Information and Automation (ICIA), 2016, pp. 1387–1391.
[12] K. Ueki, R. Sato, A. Ming, M. Shimojo, M. Hammadi, and J.-
Y. Choley, “Development of knee joint mechanism with variable transmission and joint stop for bipedal robot inspired by human structure,” in 2020 21st International Conference on Research and Education in Mechatronics (REM), 2020, pp. 1–6.
[13] G. van Oort, R. Carloni, D. J. Borgerink, and S. Stramigioli, “An energy efficient knee locking mechanism for a dynamically walking robot,” in 2011 IEEE International Conference on Robotics and Automation, 2011, pp. 2003–2008.
[14] S. Anderson, M. Wisse, C. Atkeson, J. Hodgins, G. Zeglin, and
B. Moyer, “Powered bipeds based on passive dynamic principles,” in 5th IEEE-RAS International Conference on Humanoid Robots, 2005., 2005, pp. 110–116.
[15] T. Mikolajczyk, E. Mikołajewska, H. F. N. Al-Shuka, T. Malinowski,
A. Kłodowski, D. Y. Pimenov, T. Paczkowski, F. Hu, K. Giasin,
D. Mikołajewski, and M. Macko, “Recent advances in bipedal walking robots: Review of gait, drive, sensors and control systems,” Sensors, vol. 22, no. 12, 2022.
[16] Y. Huang, B. Vanderborght, R. Van Ham, Q. Wang, M. Van Damme,
G. Xie, and D. Lefeber, “Step length and velocity control of a dynamic bipedal walking robot with adaptable compliant joints,” IEEE/ASME Transactions on Mechatronics, vol. 18, no. 2, pp. 598–611, 2013.
[17] M.-H. Park and B.-K. Cho, “Design of new drive mechanism for dynamic movement of humanoid robot legs,” in 2023 IEEE-RAS 22nd International Conference on Humanoid Robots (Humanoids), 2023, pp. 1–8.
[18] M. Plooij, G. Mathijssen, P. Cherelle, D. Lefeber, and B. Vanderborght, “Lock your robot: A review of locking devices in robotics,” IEEE Robotics & Automation Magazine, vol. 22, no. 1, pp. 106–117, 2015.
[19] A. G. Baines, “Knee design for a bipedal walking robot based on a passive-dynamic walker,” BSc report, Massachusetts Institute of Technology, 2005.
[20] J. Reher, W.-L. Ma, and A. Ames, “Dynamic walking with compliance on a cassie bipedal robot,” 2019 18th European Control Conference (ECC), pp. 2589–2595, 2019.
[21] D. J. Braun, J. E. Mitchell, and M. Goldfarb, “Actuated dynamic walking in a seven-link biped robot,” IEEE/ASME Transactions on Mechatronics, vol. 17, no. 1, pp. 147–156, 2012.
[22] K. B. Trifonov, G. Enriquez, and S. Hashimoto, “Design issues and applications for a passive-dynamic walker,” in International Conference on Multimedia and Ubiquitous Engineering, 2009.
[23] K. B. Trifonov and S. Hashimoto, “Active knee-release mechanism for passive-dynamic walking machines and walking cycle research,” in 2008 IEEE/RSJ International Conference on Intelligent Robots and Systems, 2008, pp. 179–184.
[24] A. A. A. Reynolds, “Design and control of a clutch for a minimallyactuated biped based on the passive-dynamic simple walker,” BSc report, Massachusetts Institute of Technology, 2006.
[25] RE-140RA, Mabuchi Motor Co., Ltd, 2020. [Online]. Available: https: //www.mabuchi-motor.co.jp/motorize/branch/motor/pdf/re_140ra.pdf
[26] SH-K0730S, | Shih | Shin | Technology | Co., | Ltd., | 2023.
[Online]. Available: https://www.solenoids.com.tw/document-detail/0/product-data-SH-K0730/ (https://www.solenoids.com.tw/document-detail/0/product-data-SH-K0730/)
[27] X. Liu, X. Zang, Y. Zhu, Y. Liu, and J. Zhao, “System overview and walking dynamics of a passive dynamic walking robot with flat feet,” Advances in Mechanical Engineering, vol. 7, no. 12, p. 1687814015620967, 2015.

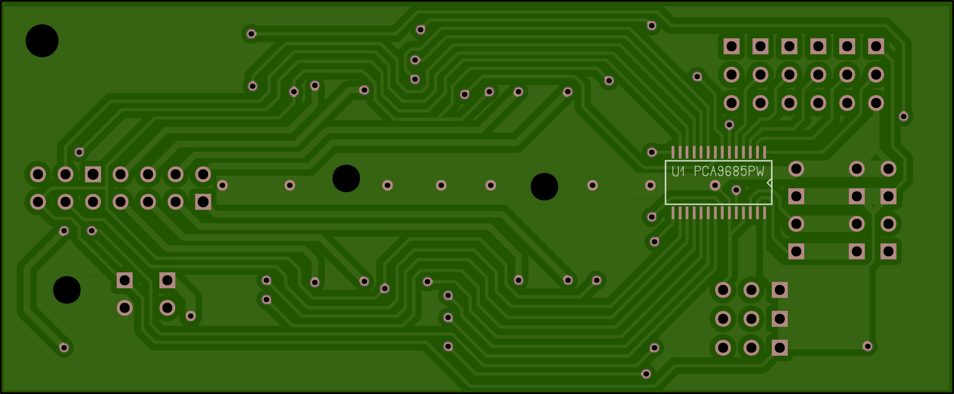
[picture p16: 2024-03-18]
electronics/DRIVER_KNEE_V5/Bottom Green.png

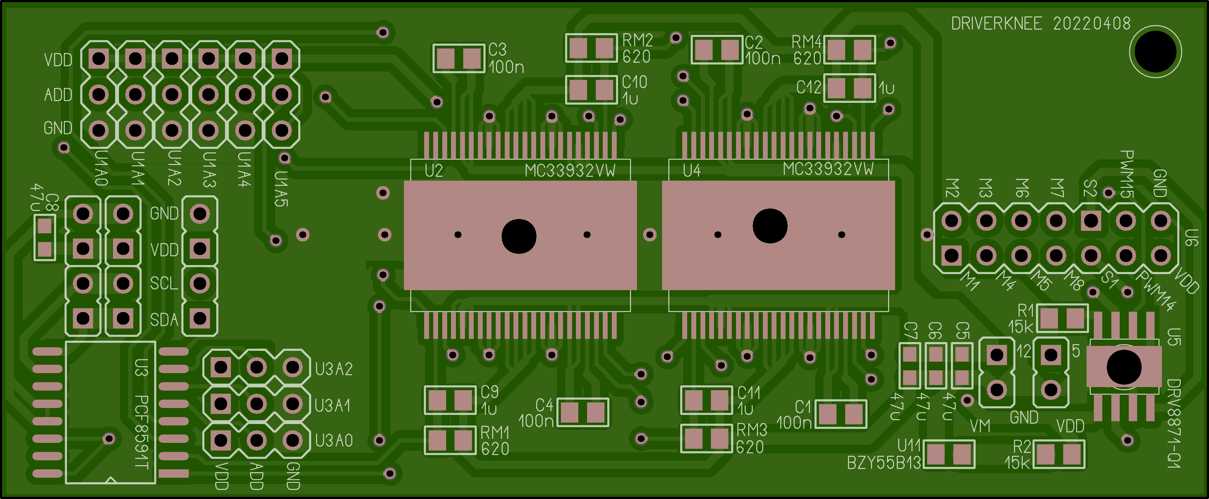
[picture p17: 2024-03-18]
electronics/DRIVER_KNEE_V5/Top Green.png

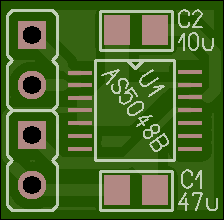
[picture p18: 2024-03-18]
electronics/ENCODER/Top Green.png

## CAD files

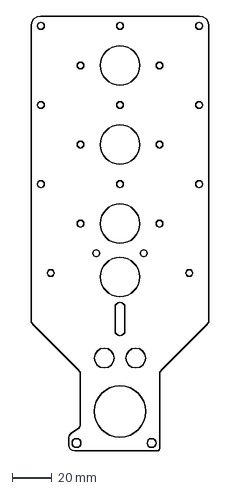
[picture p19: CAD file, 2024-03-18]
CAD/DXF/KNEE_BRACE_OUTER_V3.DXF
90.0 x 220.0 mm

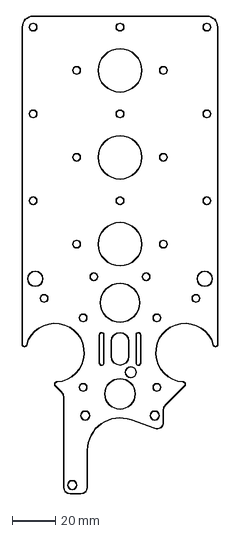
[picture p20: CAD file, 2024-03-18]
CAD/DXF/KNEE_BRACE_3.DXF
90.0 x 220.0 mm

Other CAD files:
CAD/LEG_ASSY_2_PUBLIC.x_t

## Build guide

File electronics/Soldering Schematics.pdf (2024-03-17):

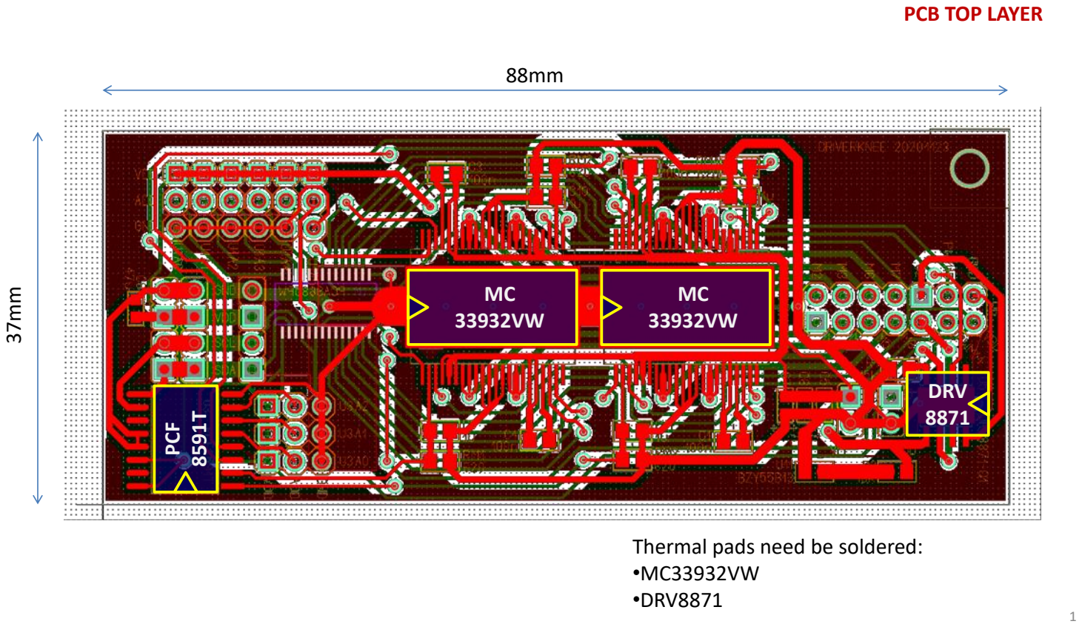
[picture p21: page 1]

1

88mm

MC
33932VW

PCF

8591T

37mm

DRV
8871

PCB TOP LAYER

MC
33932VW

Thermal pads need be soldered: •MC33932VW
•DRV8871

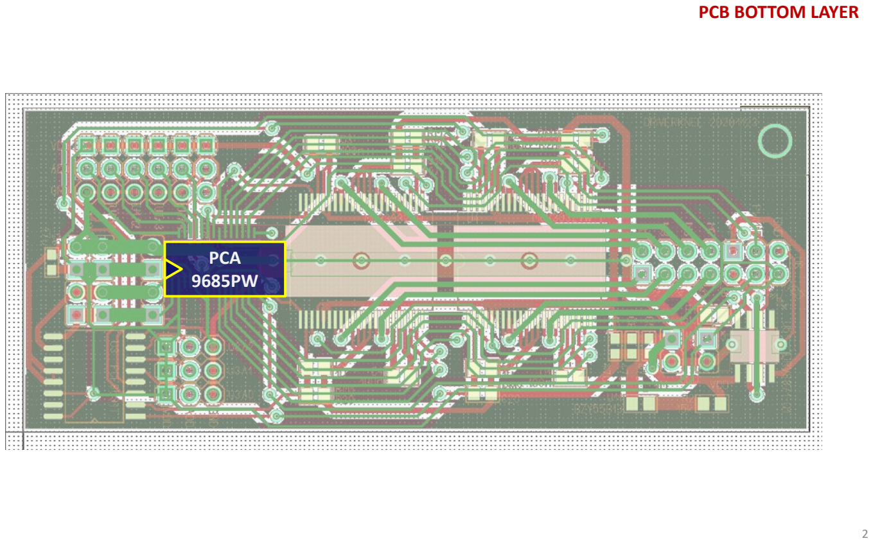
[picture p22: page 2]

2

PCA
9685PW

PCB BOTTOM LAYER

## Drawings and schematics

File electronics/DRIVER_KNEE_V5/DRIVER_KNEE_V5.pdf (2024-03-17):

## Cheng-Yueh Liu DRIVER_KNEE rev: 15 March 2024

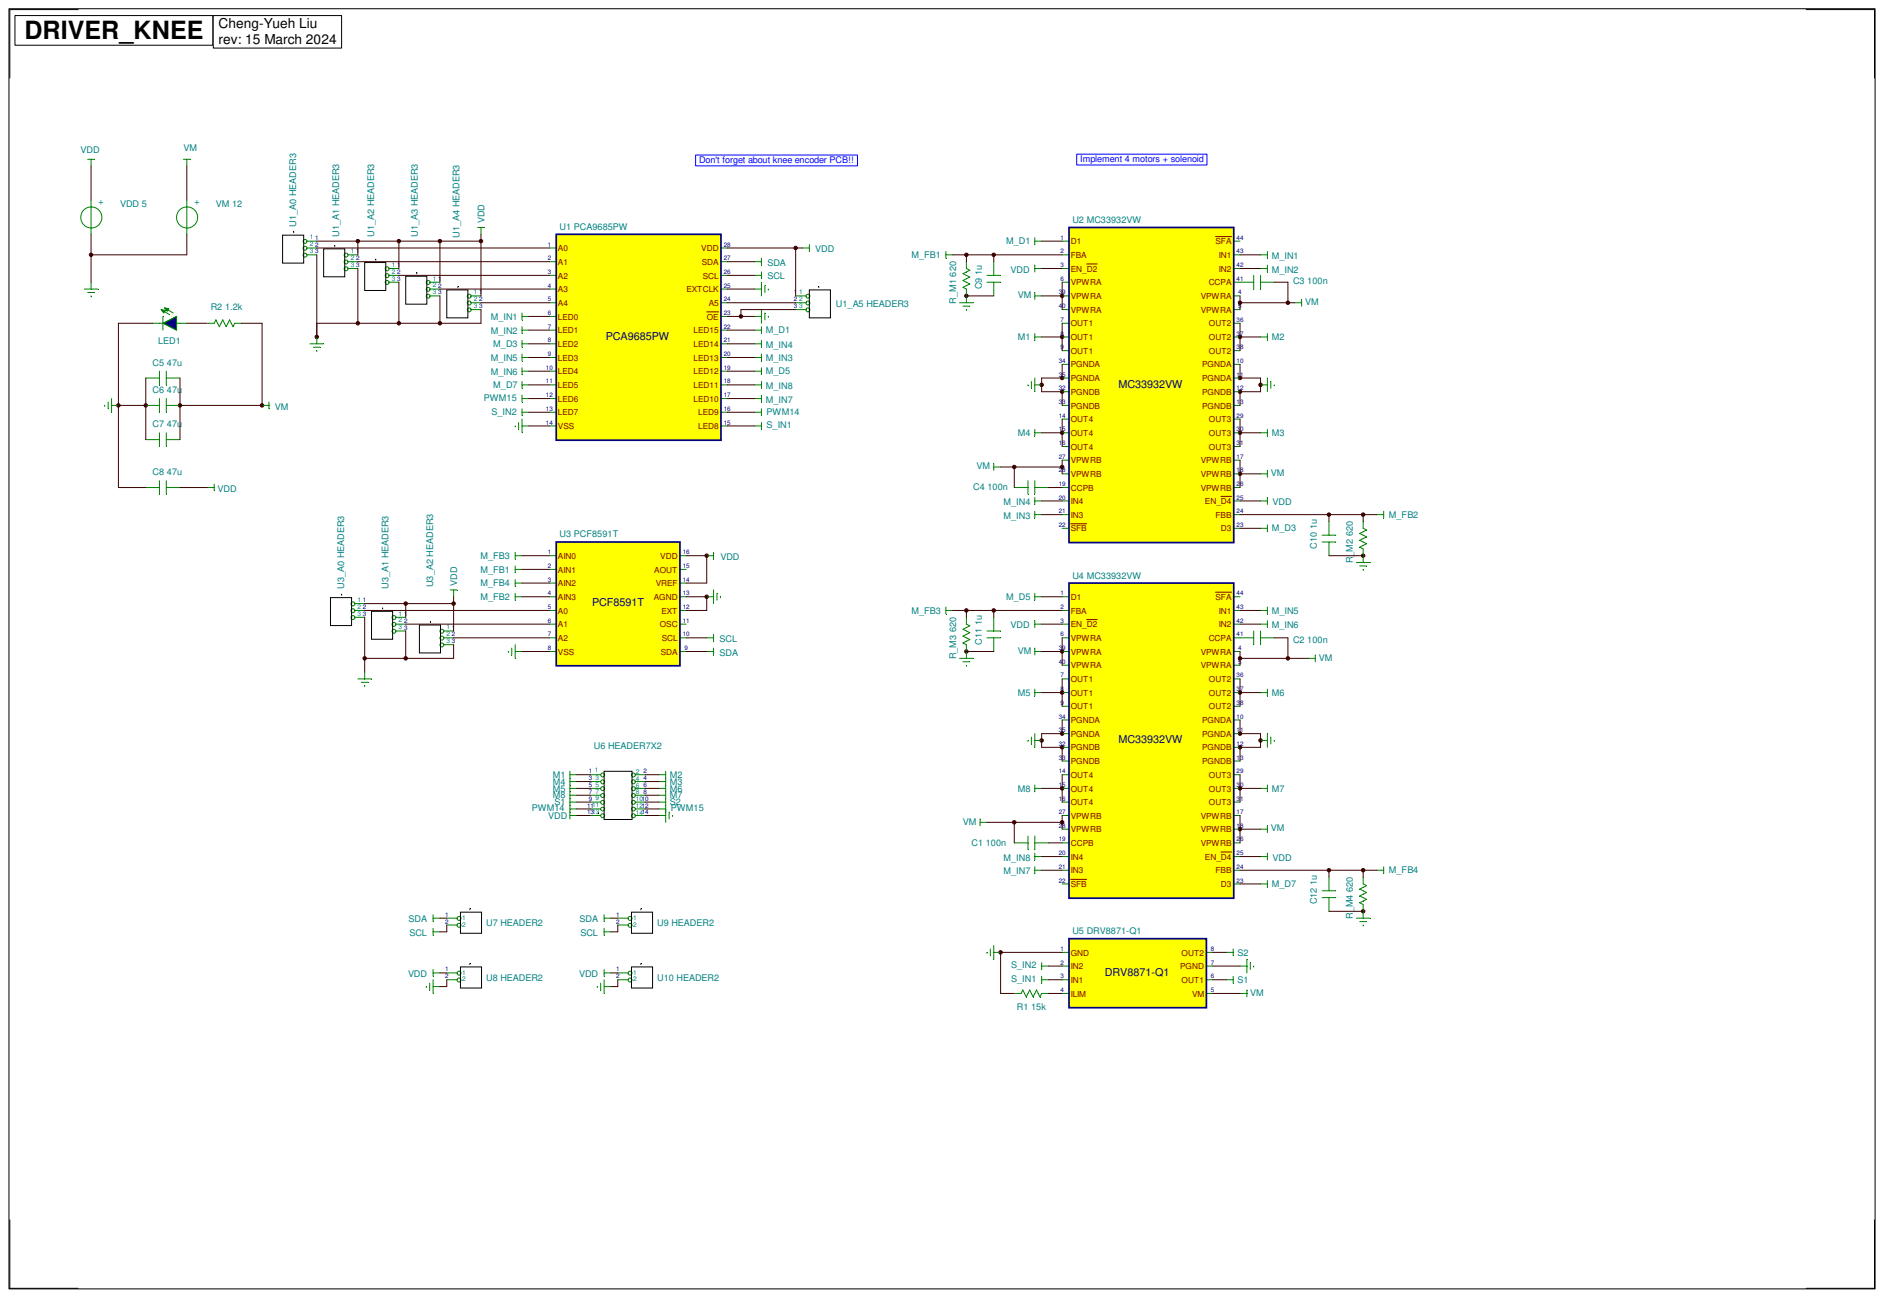
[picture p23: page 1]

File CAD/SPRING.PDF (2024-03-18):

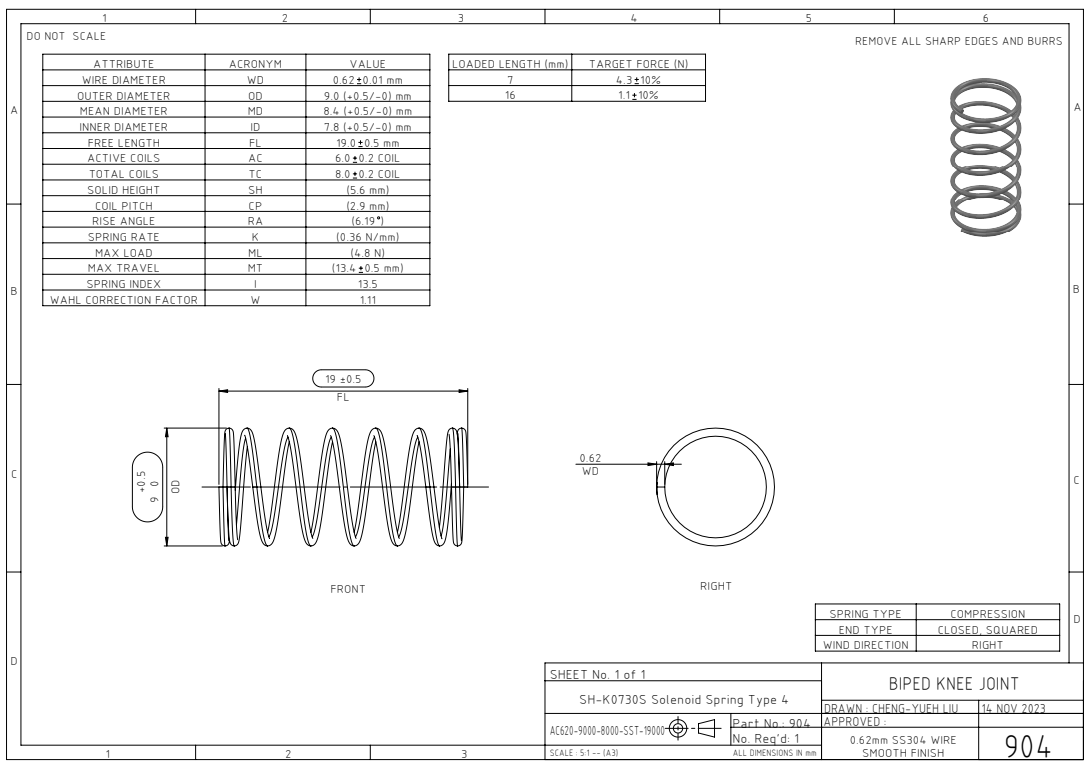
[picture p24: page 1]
WIRE DIAMETER; FREE LENGTH; ACTIVE COILS; 0.2 COIL; TOTAL COILS; MAX TRAVEL; LOADED LENGTH (mm); TARGET FORCE (N); SCALE : 5:1 -- (A3); ALL DIMENSIONS IN mm

DO NOT SCALE

REMOVE ALL SHARP EDGES AND BURRS

OUTER DIAMETER | OD | 9.0 (+0.5/-0) mm
MEAN DIAMETER | MD | 8.4 (+0.5/-0) mm
INNER DIAMETER | ID | 7.8 (+0.5/-0) mm

SOLID HEIGHT | SH | (5.6 mm)
COIL PITCH | CP | (2.9 mm)
RISE ANGLE | RA | (6.19 )
SPRING RATE | K | (0.36 N/mm)
MAX LOAD | ML | (4.8 N)

SPRING INDEX | I | 13.5
WAHL CORRECTION FACTOR | W | 1.11

SPRING TYPE | COMPRESSION
END TYPE | CLOSED, SQUARED
WIND DIRECTION | RIGHT

SHEET No. 1 of 1
SH-K0730S Solenoid Spring Type 4
No. Req'd: 1 AC620-9000-8000-SST-19000

BIPED KNEE JOINT

DRAWN : CHENG-YUEH LIU | 14 NOV 2023
0.62mm SS304 WIRE SMOOTH FINISH | 904

Part No.: 904 | APPROVED :

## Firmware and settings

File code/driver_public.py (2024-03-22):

import smbus, time, threading

# Registers/etc:
#PCA9685_ADDRESS    = 0x40
MODE1              = 0x00
MODE2              = 0x01
SUBADR1            = 0x02
SUBADR2            = 0x03
SUBADR3            = 0x04
PRESCALE           = 0xFE

LED_LIST = [i for i in range(6,67,4)]

ALL_LED_ON_L       = 0xFA
ALL_LED_ON_H       = 0xFB
ALL_LED_OFF_L      = 0xFC
ALL_LED_OFF_H      = 0xFD

# MODE 1 bits
RESTART            = 0x80
SLEEP              = 0x10
ALLCALL            = 0x01

# MODE 2 bits
INVRT              = 0x10
OUTDRV             = 0x04

MOTOR_ALLCALL_ADD = 0x70
MOTOR_PAIR_NO = 0


def motor_reg_id(motor_pair_no, driver = 0):
    
    # int 0 to 3
    # Returns register adress tuple for motor pair (Dn, IN1n, IN2n)
    # (M1, M2), (M3, M4), (M5, M6), (M7, M8) IN THIS ORDER!

    # Identify the first address of 4 registers per LED PWM
    if driver is 0:
        motor_reg_dic = {0: (LED_LIST[15], LED_LIST[0], LED_LIST[1]),
                         1: (LED_LIST[2], LED_LIST[13], LED_LIST[14]),
                         2: (LED_LIST[12], LED_LIST[3], LED_LIST[4]),
                         3: (LED_LIST[5], LED_LIST[10], LED_LIST[11]),
                         4: (None, LED_LIST[8], LED_LIST[7])}
    if driver is 1:
        motor_reg_dic = {key: value for (key, value) in
                         [(3-i,(None, LED_LIST[i*2], LED_LIST[i*2+1])) for i in range(4)]}
    
    return motor_reg_dic.get(motor_pair_no, None)


def solenoid_reg_id():
    
    # Returns register adress tuple for solenoid pair
    # (S_IN1, S_IN2)
    
    return motor_reg_id(4)[1:]


def set_PWM_freq(PCA9685_add, freq):
    
    # freq in Hz
    # bound between 0x03 (1526 Hz) and 0xFF (24 Hz)
    prescaleval = max(0x03, min(0xFF, int(25000000.0/(4096.0 * freq) - 1.0)))
    
    # sleep first before updating prescaler
    oldmode = bus.read_byte_data(PCA9685_add, MODE1)
    newmode = (oldmode & 0x7F) | 0x10    # sleep
    bus.write_byte_data(PCA9685_add, MODE1, newmode)  # go to sleep
    
    # update prescaler
    bus.write_byte_data(PCA9685_add, PRESCALE, prescaleval) 
    
    # wake + reinstate mode before sleep
    bus.write_byte_data(PCA9685_add, MODE1, oldmode)
    time.sleep(0.005) # SLEEP = 0 for min 500 us before RESTART bit = 1
    bus.write_byte_data(PCA9685_add, MODE1, oldmode | 0x80) # restart with orig LED vals
    
    return None


def write_LED_data(PCA9685_add, reg_add, led_times):
    
    # reg_add = address of first register address of relevant LED port
    # led_on, led_off = 0 to 4096 inclusive
    (led_on, led_off) = led_times
    bit_str = led_off << 16 | led_on
    data_list = []
    
    for i in range(4):
        data_list.append(bit_str & 0b11111111)
        bit_str = bit_str >> 8
    
    try_count = 0
    while try_count < 50:
        try:
            bus.write_i2c_block_data(PCA9685_add, reg_add, data_list)
            break
        except: try_count += 1

    return None


def set_motor(PCA9685_add, motor_pair_no, mode, duty, direction, delay = 0, disable = 0, driver = 0):
    
    # Modes when PWM is low:
    # 0: Brake low side slow decay
    # 1: Brake high side slow decay
    # direction: 0 forward, 1 reverse
    # duty: 0.0 to 1.0 float
    # delay: in ticks (0 to 4095)
    
    (D_add, IN1_add, IN2_add) = motor_reg_id(motor_pair_no, driver)
    if D_add is not None: write_LED_data(PCA9685_add, D_add, [0, 4096][::-2*disable+1]) # Enable/disable
    
    [high_dur, low_dur] = [round(4096*i) for i in (duty, 1-duty)][::-2*mode+1]
    
    # Always start with LED_ON
    if duty == 0:
        write_LED_data(PCA9685_add, IN1_add, [0, 4096][::-2*mode+1])
        write_LED_data(PCA9685_add, IN2_add, [0, 4096][::-2*mode+1])
    elif 0 < duty <=1.0:
        if 0 < duty < 1.0: [on_time, off_time] = [delay, (delay + high_dur) % 4096]
        if duty == 1.0: [on_time, off_time] = [4096, 0][::-2*mode+1]
        write_LED_data(PCA9685_add, [IN1_add, IN2_add][mode ^ direction], [on_time, off_time]) # PWM this LED
        write_LED_data(PCA9685_add, [IN2_add, IN1_add][mode ^ direction], [0, 4096][::-2*mode+1]) # Fix the other LED   
    
    return None


def stop_knee(mode, PCA9685_add):
    
    for motor_pair_no in range(4): set_motor(PCA9685_add, motor_pair_no, mode, 0, 0)
    
    return None


def set_knee(PCA9685_add, func, duty, duty_max = 0.25, duty_lambda = 1, duration = None, mode = 0):
    
    # Function:
    # 0: Forward (bend knee)
    # 1: Reverse
    # 2: Gear up
    # 3: Gear down
    # duty_lambda: duty prescaler to reduce gear upwards force
    #              during forward or reverse operations
    
    duty = min(duty, duty_max)
    for motor_pair_no in range(4):
        direction = [motor_pair_no>=2, motor_pair_no<2, 0, 1][func]
        duty_scale = [[duty_lambda, 1][direction], 1][func>=2]
        set_motor(PCA9685_add, motor_pair_no, mode, duty_scale*duty, direction)
    
    # turn off motor after a while if duration is set
    if duration is not None:
        stop_motors = threading.Timer(duration, lambda: stop_knee(mode, PCA9685_add))
        stop_motors.start()
    
    return None


def set_solenoid(PCA9685_add, mode, duration=0.1, lock_duty = 1.0, unlock_duty = 0.5):
    
    # mode: 0 lock, 1 unlock
    # unlocking voltage must be below 8.0V; unrestricted locking voltage
    set_motor(PCA9685_add, 4, 0, [lock_duty, unlock_duty][mode], mode)
    stop_solenoid = threading.Timer(duration, lambda: set_motor(PCA9685_add, 4, 0, 0, 0))
    stop_solenoid.start()
    
    return None


def initialize(PCA9685_add):
    
    bus.write_byte_data(PCA9685_add, MODE1, 0b00100001) # MODE 1 default
    bus.write_byte_data(PCA9685_add, MODE2, 0b00001100) # MODE 2 default
    bus.write_byte_data(PCA9685_add, ALL_LED_ON_L, 0) # Turn all LEDs off
    bus.write_byte_data(PCA9685_add, ALL_LED_ON_H, 0) # Turn all LEDs off
    bus.write_byte_data(PCA9685_add, ALL_LED_OFF_L, 0) # Turn all LEDs off
    bus.write_byte_data(PCA9685_add, ALL_LED_OFF_H, 16) # Turn all LEDs off
    set_PWM_freq(PCA9685_add, 1526)
    
    return None


bus = smbus.SMBus(1)

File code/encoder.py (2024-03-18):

import smbus
from math import pi as pi

ENC_ADD = 0x40

REG_ANG_1 = 0xFE
REG_ANG_2 = 0xFF
REG_I2C_SLAVE_ADD = 0x15
REG_PRO_CNTL = 0x03


def read_angle(output = 'bit', offset = 0, remap = True, enc_add = ENC_ADD):
	
    # output: 'bits' returns raw bit value 0-16383, deg or rad
    
    valid = False
    while not valid:
        try:
            ang_1, ang_2 = bus.read_byte_data(enc_add, REG_ANG_1), \
                           bus.read_byte_data(enc_add, REG_ANG_2)
            valid = True
        except IOError: valid = False
    
    bit_val = ((ang_1 << 6) + ang_2 - offset) % 2**14
    if remap: bit_val = (lambda x: x - 2**14 if x > 2**13 else x)(bit_val)
    
    return {'bit': bit_val,
            'deg': bit_val * 360/2**14,
            'rad': bit_val * 2*pi/2**14}.get(output, None)


def otp_address(check, enc_otp_cont, enc_old_add = ENC_ADD):
    
    # burns OTP subaddress
    # enc_otp_cont: 4 bit OTP programmable subaddress
    # READ DATASHEET THOROUGHLY BEFORE EXECUTING PROGRAM

    if check != 'holyroly': return None

    import time

    # Set new I2C slave address
    bus.write_byte_data(enc_old_add, REG_I2C_SLAVE_ADD, enc_otp_cont)

    # Enable special programming mode
    ENC_NEW_ADD = 0b1000000 | (enc_otp_cont << 2)
    bus.write_byte_data(ENC_NEW_ADD, REG_PRO_CNTL, 0xFD)
    time.sleep(0.01)

    # Enable automatic programming procedure
    bus.write_byte_data(ENC_NEW_ADD, REG_PRO_CNTL, 0x08)
    time.sleep(0.01)

    # Disable special programming mode
    bus.write_byte_data(ENC_NEW_ADD, REG_PRO_CNTL, 0x00)
    time.sleep(0.01)

    return None


bus = smbus.SMBus(1)
